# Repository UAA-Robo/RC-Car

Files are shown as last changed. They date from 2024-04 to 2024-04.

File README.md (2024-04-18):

# RC-Car
This is a RC Car Workshop tutorial. To create this car, follow the below steps.

## BOM (Bill of Materials)

| Name | Number Units |
|---|---|
| PLA Filament | - |
| ESP32-WROOM-32D | 1 |
| USB Micro Data Cables | 1 |
| Jumper Wire | 6 |
| TT Motor Dual DC Motor | 4 |
| DRV8833 Motor Drive Module (Pins may need to be soldered)  | 1 |
| AA Battery | 4 |
| 4 AA Battery Holder | 1 |
| 9V Battery | 1 |
| 9V Battery Connector | 1 |
| Small Breadboard | 1 |
| Zip Ties | 4 |
| Hot Glue or Tape | - |

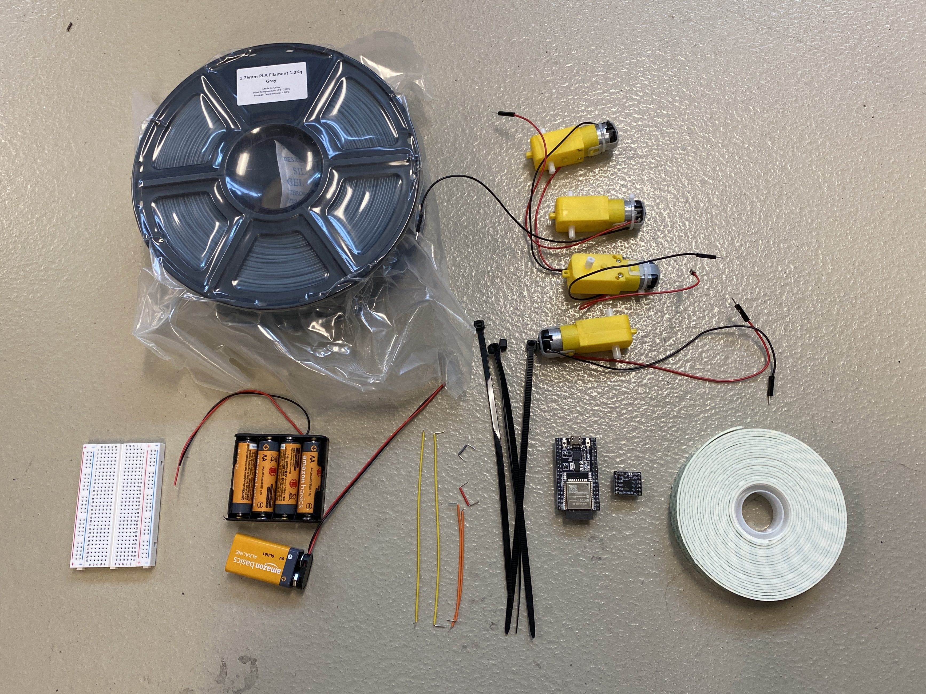
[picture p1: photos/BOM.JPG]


## Instructions

### 1. 3D Print your parts.
3D print the chassis (CAD/chassis.stl) and 4 wheels (CAD/wheel.stl). Optionally, you can print fun ad-ons/mods (CAD/Mods/...).

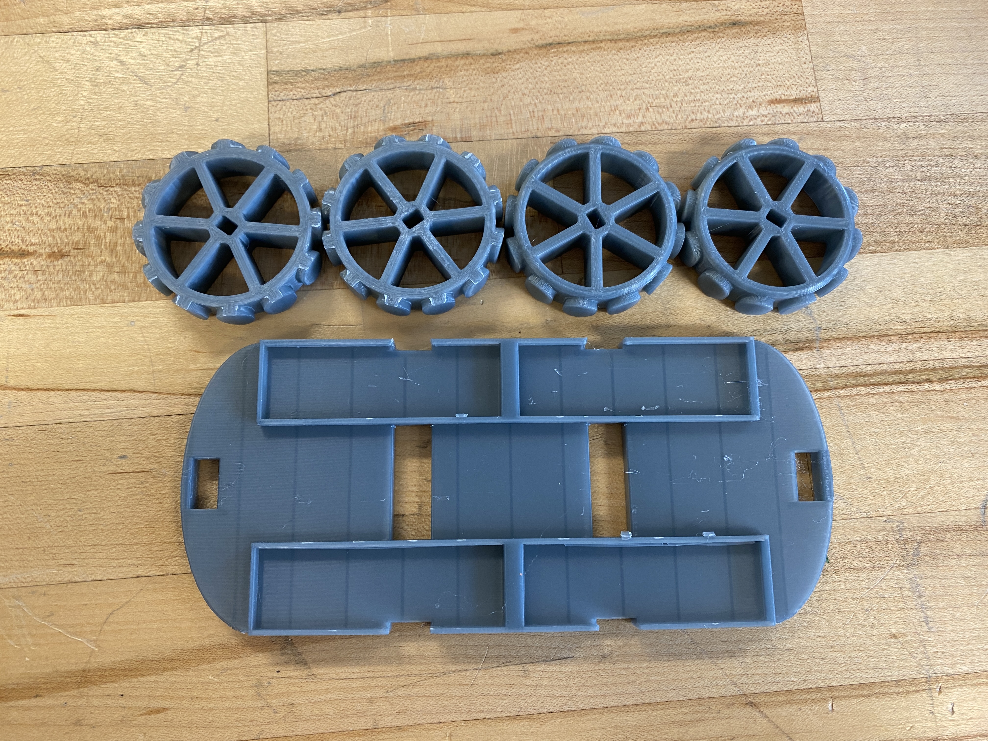
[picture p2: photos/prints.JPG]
3D prints


### 2. Attach your motors and wheels
Use zipties to attach your motors to the bottom of your chassi. Note: be careful of motor orientation. Add the wheels to the motors.

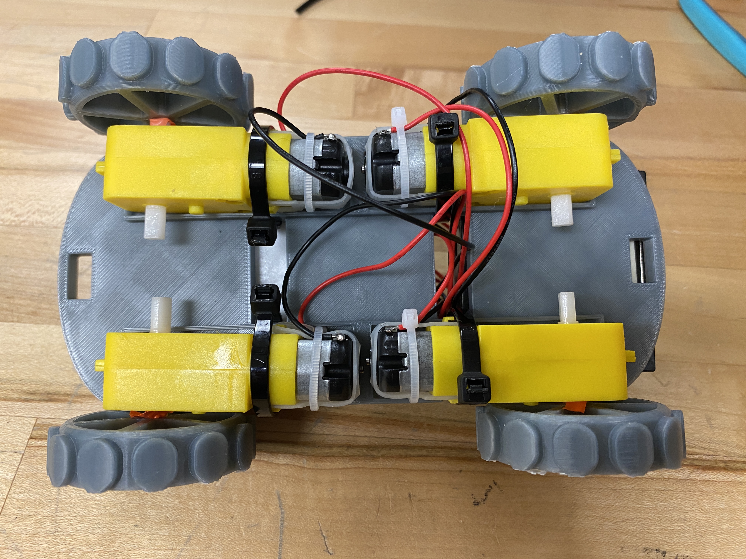
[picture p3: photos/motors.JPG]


### 3.  Wire your components
Flip over the chassi, add the breadboard, and batttery holders using tape or hot glue to secure as necessary. Wire the components using the following wiring diagram. Do NOT add the batteries yet.

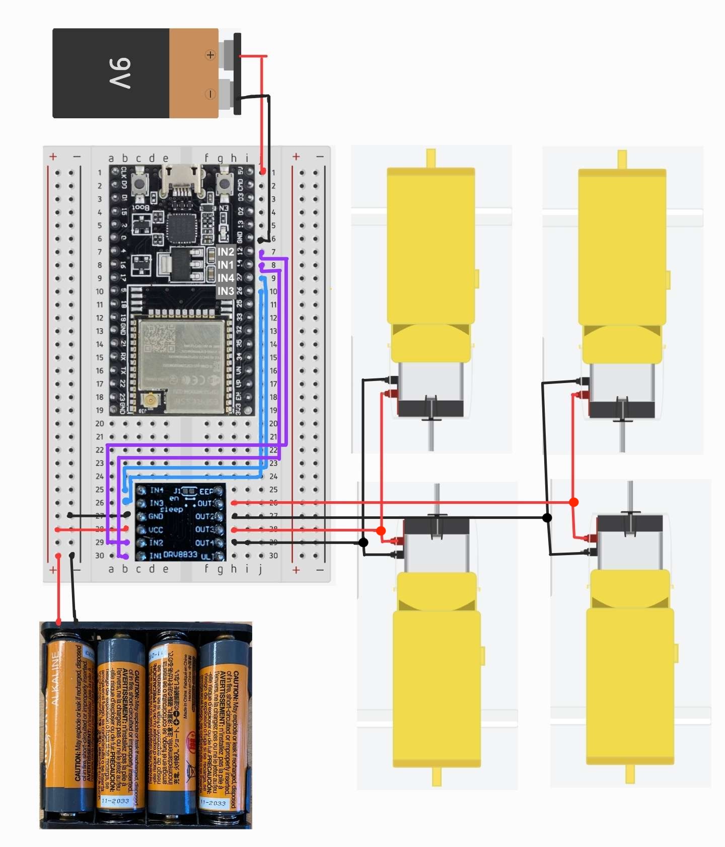
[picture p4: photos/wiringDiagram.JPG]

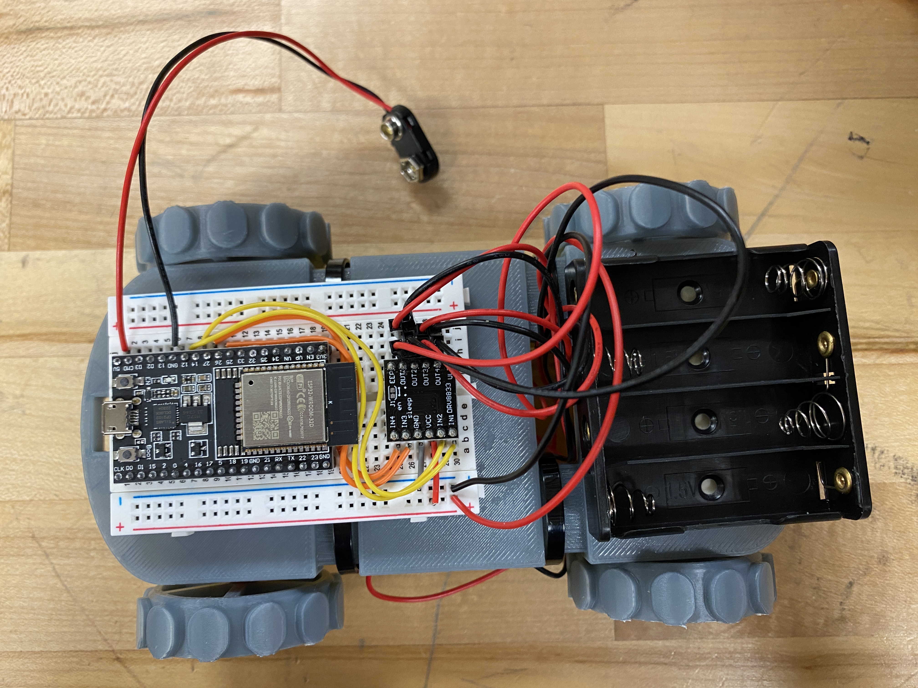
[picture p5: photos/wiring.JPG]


### 4.  Upload Code to your ESP32.
a. Make sure the Arduino IDE and UART Driver is installed on your computers:

* Arduino IDE: https://www.arduino.cc/en/software	

* UART Driver: https://www.silabs.com/developers/usb-to-uart-bridge-vcp-drivers?tab=downloads		
    * On Windows, download/extract CP210x VCP Windows and run CP210xVCPInstaller_x64. 
    * On Mac, download/extract CP210x VCP Mac OSX Driver and run SiLabasUSBDriverDisk.dmg

b. In the Arduino IDE, go to Tools > Board > Board Manger. Type in ESP32 and install esp32 by Espressif. 

c. Plug in the ESP32 to your computer and click on the new port that is added in the white box in the top bar. A window with “Select Other Board and Port” should pop up. Under boards, filter and select “ESP32-WROOOM-DA Module”. Then click okay.

d. Now time to code! Copy/Paste one of the following programs into the editor and make sure save it is saved: 

* Program different functions to turn the motors: https://github.com/UAA-Robo/RC-Car/blob/main/code/rc_motor_functions/rc_motor_functions.ino

* Program the code to be remote controlled w/ bluetooth: https://github.com/UAA-Robo/RC-Car/blob/main/code/rc_remote_control/rc_remote_control.ino

e. Make sure the ESP32 is plugged into the computer and press the arrow to upload to the ESP32. The program will immediately begin.

f. If you’re running the remote control code (d.ii), you will also need to download the RemoteXY (https://remotexy.com/en/download/) app

* Open the app and click “+” > “Bluetooth LE”. Select your “myESP32” as your device (unless you change it in the code).You should then connect

### 5. Add battteries.
Unplug the ESP32, double check your wiring, and add batteries. Once lights turn on both the ESP32 and motor driver, your code is running.

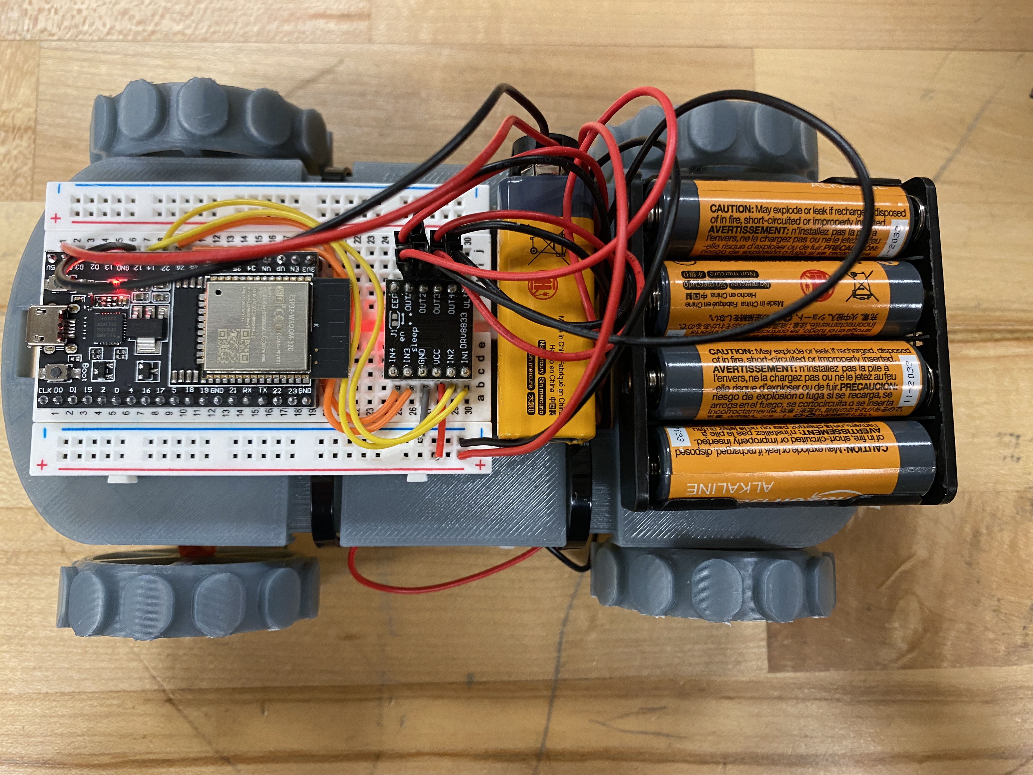
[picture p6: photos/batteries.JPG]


## Troubleshooting Tips
* No wheels are turning and no lights are showing on the ESP32 or Motor Drivers.
    * Check that your wiring still matches the diagram (especially the battery connections).
    * Replace all the batteries.
* Wheels not turning the right direction, or some are not turning:
    * Check that your wiring still matches the diagram. 
    * Check that everything is connected fully and the motor wiring still touches the motor tabs.
* Bluetooth keeps disconnecting and lights on the Motor Drivers flicker.
    * One of the batteries may be low on voltage. Try replacing one or all of the  batteries

Credit: Mya Schroder, Jaren Ramirez, Reese Cochran

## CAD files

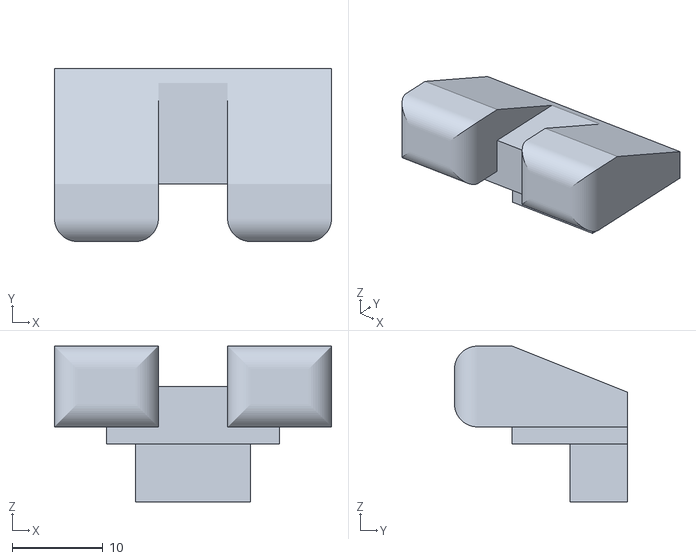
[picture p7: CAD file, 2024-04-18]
CAD/Mods/headlight.stl
30.5 x 19.1 x 17.1

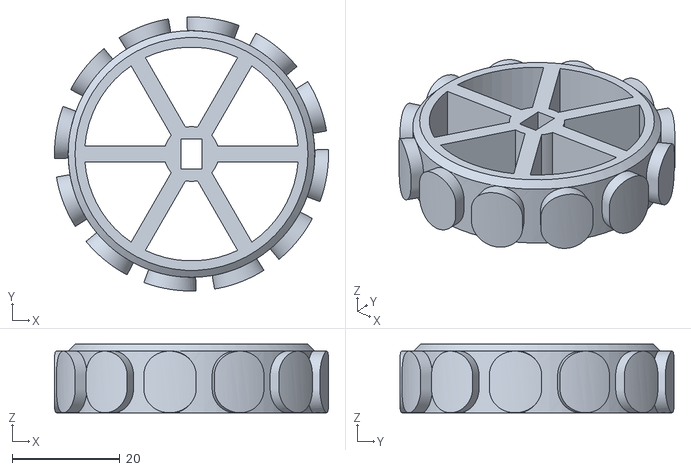
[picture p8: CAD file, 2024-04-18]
CAD/wheel.stl
50.8 x 50.8 x 12.7

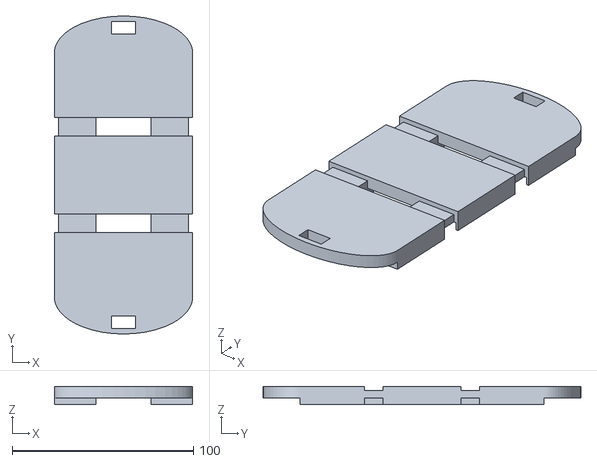
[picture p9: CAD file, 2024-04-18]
CAD/chassis.stl
76.2 x 175.3 x 10.2

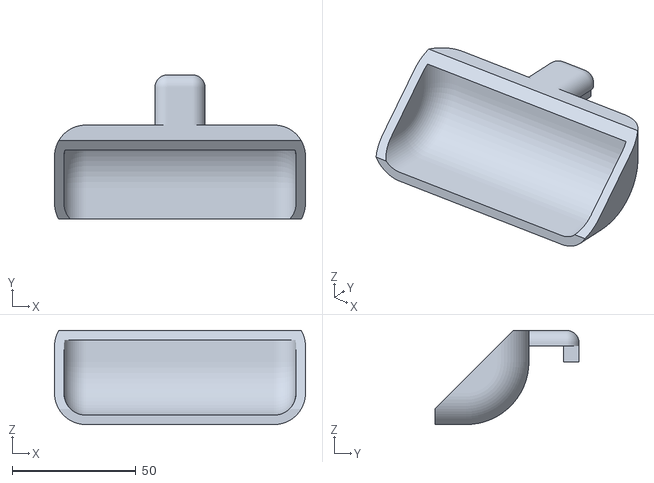
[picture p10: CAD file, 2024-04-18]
CAD/Mods/plow.stl
101.6 x 58.4 x 38.1

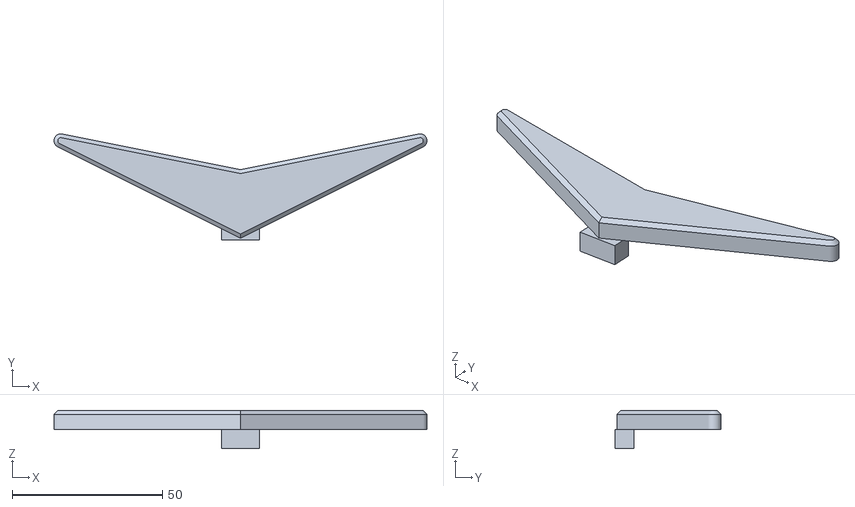
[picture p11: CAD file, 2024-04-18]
CAD/Mods/wing.stl
124.3 x 35.4 x 12.7

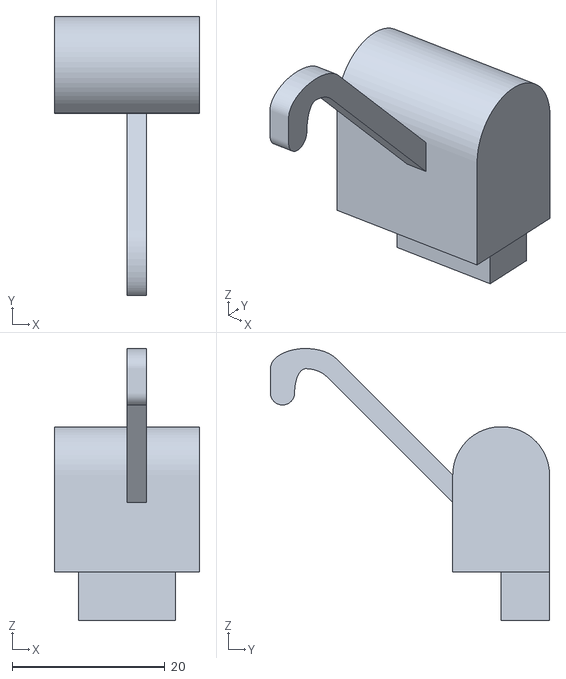
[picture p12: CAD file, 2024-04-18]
CAD/Mods/towHook.stl
19.1 x 36.6 x 35.6

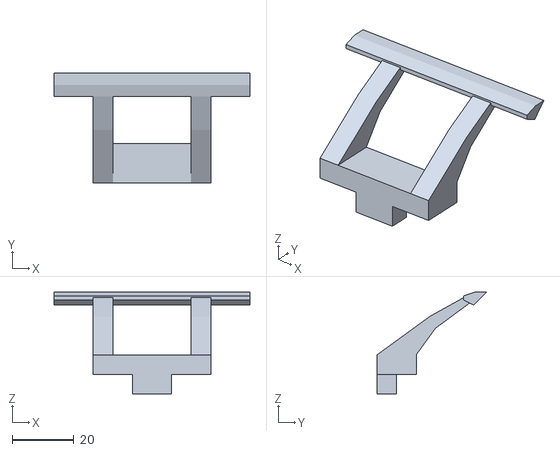
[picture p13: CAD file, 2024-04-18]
CAD/Mods/wing2.stl
63.5 x 35.6 x 33.0

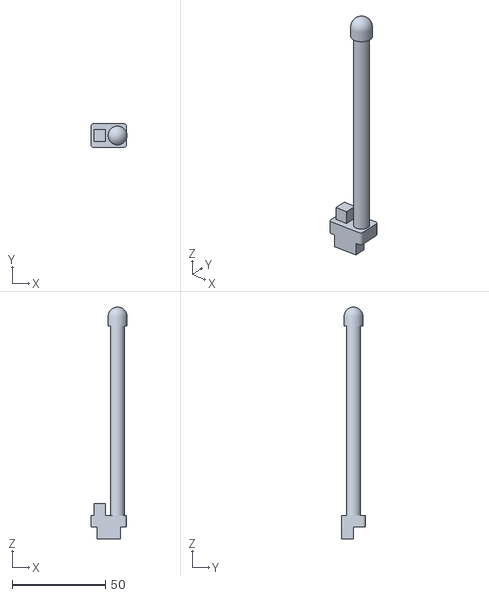
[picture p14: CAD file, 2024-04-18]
CAD/Mods/antenna.stl
19.4 x 12.7 x 124.5

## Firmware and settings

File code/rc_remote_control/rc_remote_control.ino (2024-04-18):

/*   
   This source code of graphical user interface 
   has been generated automatically by RemoteXY editor.
   To compile this code using RemoteXY library 3.1.11 or later version 
   download by link http://remotexy.com/en/library/
   To connect using RemoteXY mobile app by link http://remotexy.com/en/download/                   
     - for ANDROID 4.11.4 or later version;
     - for iOS 1.9.1 or later version;
    
   This source code is free software; you can redistribute it and/or
   modify it under the terms of the GNU Lesser General Public
   License as published by the Free Software Foundation; either
   version 2.1 of the License, or (at your option) any later version.    
*/

//////////////////////////////////////////////
//        RemoteXY include library          //
//////////////////////////////////////////////

// you can enable debug logging to Serial at 115200
//#define REMOTEXY__DEBUGLOG  

// RemoteXY select connection mode and include library 
#define REMOTEXY_MODE__ESP32CORE_BLE
#include <BLEDevice.h>

#include <RemoteXY.h>

// RemoteXY connection settings 
#define REMOTEXY_BLUETOOTH_NAME "MyESP"


// RemoteXY configurate  
#pragma pack(push, 1)
uint8_t RemoteXY_CONF[] =   // 87 bytes
  { 255,4,0,0,0,80,0,16,31,1,1,0,26,41,12,12,2,31,32,226,
  134,145,32,0,1,0,14,57,12,12,2,31,226,134,144,0,1,0,38,57,
  12,12,2,31,226,134,146,0,1,0,26,73,12,12,2,31,32,226,134,147,
  32,0,129,0,9,7,47,6,2,82,101,109,111,116,101,32,67,111,110,116,
  114,111,108,108,101,114,0 };
  
// this structure defines all the variables and events of your control interface 
struct {

    // input variables
  uint8_t up; // =1 if button pressed, else =0 
  uint8_t left; // =1 if button pressed, else =0 
  uint8_t right; // =1 if button pressed, else =0 
  uint8_t down; // =1 if button pressed, else =0 

    // other variable
  uint8_t connect_flag;  // =1 if wire connected, else =0 

} RemoteXY;
#pragma pack(pop)

/////////////////////////////////////////////
//           END RemoteXY include          //
/////////////////////////////////////////////


#define LEFT_MOTORS_POWER 27 //IN2
#define LEFT_MOTORS_GROUND 26 // IN1
#define RIGHT_MOTORS_POWER 12  //IN4
#define RIGHT_MOTORS_GROUND 14  //IN3


void setup() 
{
  Serial.begin(115200);
  RemoteXY_Init(); 

  // Setup pins
  pinMode(RIGHT_MOTORS_POWER, OUTPUT);
  pinMode(RIGHT_MOTORS_GROUND, OUTPUT);
  pinMode(LEFT_MOTORS_POWER, OUTPUT);
  pinMode(LEFT_MOTORS_GROUND, OUTPUT);

}

void loop() 
{ 
  RemoteXY_Handler ();
  
  // TODO you loop code
  if (RemoteXY.up == 1){
    drive_forward();
  } else if (RemoteXY.down == 1) {
    drive_backward();
  } else if (RemoteXY.left == 1) {
    turn_left();
  } else if (RemoteXY.right == 1) {
    turn_right();
  } else {
    stop();
  }

}


void drive_forward() {
    digitalWrite(RIGHT_MOTORS_POWER,HIGH);
    digitalWrite(RIGHT_MOTORS_GROUND,LOW);

    digitalWrite(LEFT_MOTORS_POWER,HIGH);
    digitalWrite(LEFT_MOTORS_GROUND,LOW);
}

void drive_backward() {
    digitalWrite(RIGHT_MOTORS_POWER,LOW);
    digitalWrite(RIGHT_MOTORS_GROUND,HIGH);

    digitalWrite(LEFT_MOTORS_POWER,LOW);
    digitalWrite(LEFT_MOTORS_GROUND,HIGH);
}

void turn_left() {
    digitalWrite(RIGHT_MOTORS_POWER,HIGH);
    digitalWrite(RIGHT_MOTORS_GROUND,LOW);

    digitalWrite(LEFT_MOTORS_POWER,LOW);
    digitalWrite(LEFT_MOTORS_GROUND,HIGH);
}

void turn_right() {
    digitalWrite(RIGHT_MOTORS_POWER,LOW);
    digitalWrite(RIGHT_MOTORS_GROUND,HIGH);

    digitalWrite(LEFT_MOTORS_POWER,HIGH);
    digitalWrite(LEFT_MOTORS_GROUND,LOW);
}

void stop(){
    digitalWrite(RIGHT_MOTORS_POWER, LOW);
    digitalWrite(RIGHT_MOTORS_GROUND, LOW);

    digitalWrite(LEFT_MOTORS_POWER, LOW);
    digitalWrite(LEFT_MOTORS_GROUND, LOW);
}

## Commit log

2024-02-03 Swapped left and right
    [rc_motor_test.ino, rc_remote_control.ino]
2024-04-11 Small mods for new motors and pwm pins
2024-04-18 Started Tutoorial
    [antenna.stl, chassis.stl, wheel.stl]
2024-04-18 Added wiring diagram and electronics.
2024-04-18 Added Reese's STLs
    [headlight.stl, plow.stl, towHook.stl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]
2024-04-18 Updated wiring diagram
